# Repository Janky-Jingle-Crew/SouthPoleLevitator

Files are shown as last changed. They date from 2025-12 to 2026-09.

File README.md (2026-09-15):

# South Pole Levitator

Janky Jingle Crew is back this Christmas as well! We are continuing with the theme of magnetic propulsion from last year, but this time for levitation! 

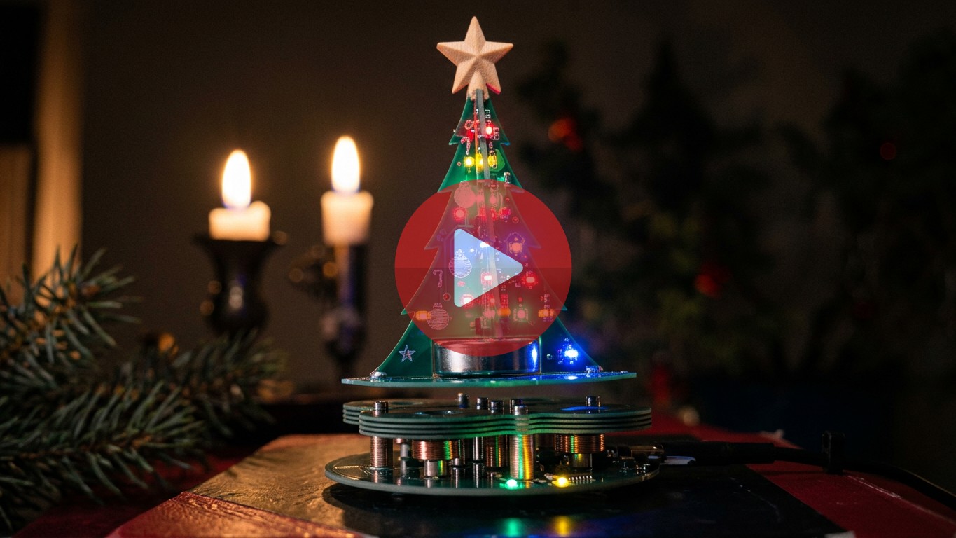
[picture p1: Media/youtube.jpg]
[](https://youtu.be/B3FScckztUA)

## Background
Magnetic levitation kits have been around for a long time, but most of them are analog designs running on 12 V. A more recent 5 V digital version by [Jonathan Lock](https://gitlab.com/e4870/maglev/-/tree/main) caught our attention and served as a big source of inspiration for this project. Our take focuses on lowering the BOM cost and making assembly easier by replacing traditional coils with PCB coils.

We were aiming to build a batch of around 50 units, so coil winding quickly became a bottleneck. That led us to PCB coils as a more scalable solution. Mounting the coils was another pain point, gluing them down and then soldering wires (like many existing kits do) felt messy. Instead, we combined the mounting and electrical connection using solderable standoffs.

We also made a (slightly unnecessary) optimization on the microcontroller side. To reduce BOM cost slightly, we chose the STM32G030, which doesn’t have an FPU, and planned to implement all control algorithms using fixed-point math. In hindsight, the time spent probably outweighed the cost savings, but at least we learned a lot about fixed-point math (and wrote terrible code) along the way.

The final result is shown below: a fully functional magnetic levitation platform made entirely from PCBs. Even the levitating tree is a PCB. Overall, the project turned out well, although there are plenty of things that could still be improved. Feel free to open an issue or mail us if you have any technical questions.

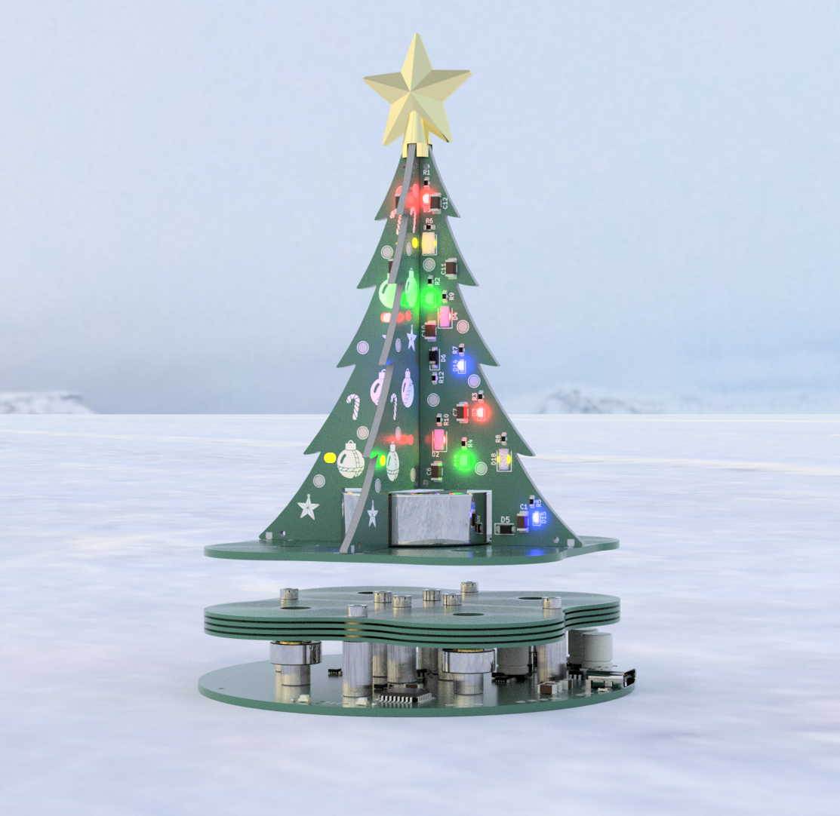
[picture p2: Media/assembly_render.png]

<!-- <img src="./Media/demo.png" width="600px"/> -->
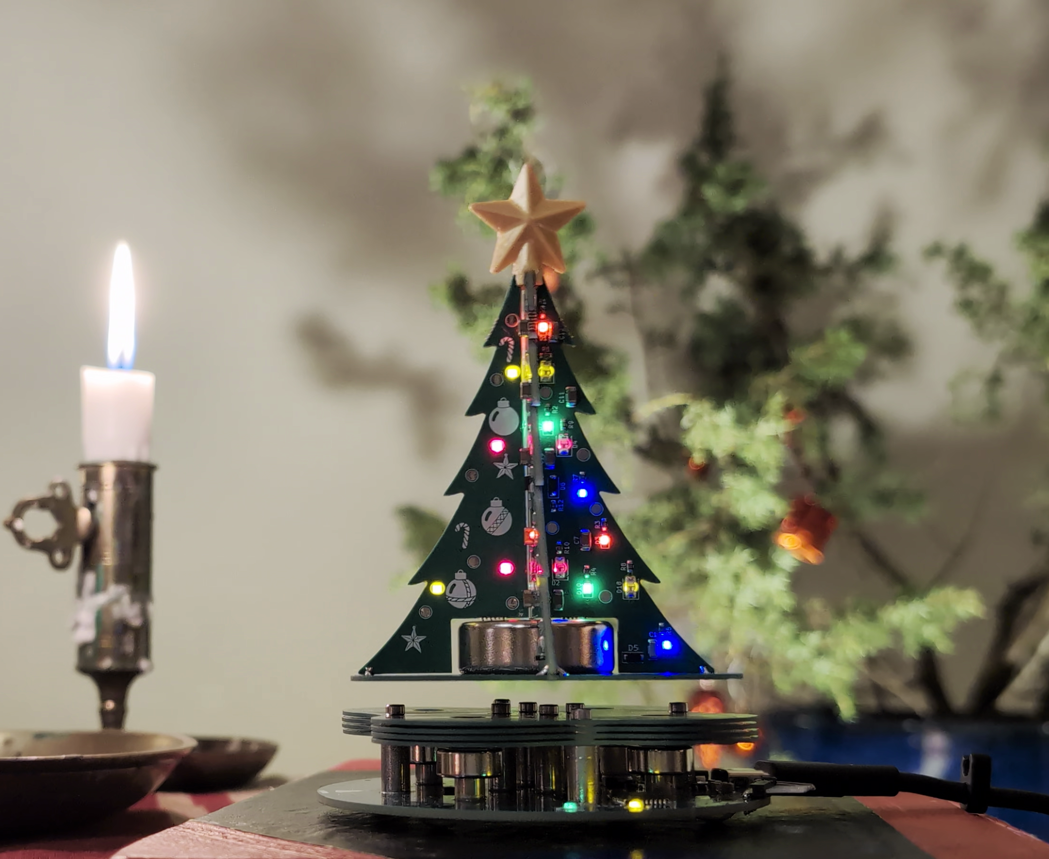
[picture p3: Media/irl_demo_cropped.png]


## User Guide

The card needs to be powered with a 5V power supply over USB-C, capable of at least 500 mA.

To levitate the tree:

1. Place the tree away from the driver board.
2. Place the driver board on a flat, nonmagnetic surface, and plug in the USB-C cable. Note that the board needs to be level when it gets power for the correct calibration. If the tree is too close, this will also affect the calibration. The calibration is complete once you hear a short beep from the coils. The status LED should also start blinking.
3. Hold the tree a few centimeters over and lower it slowly, trying to keep it centered and pointed straight up.
4. The rest is a balance between keeping the tree centered, and holding it with a loose enough grip. The tree needs to have the freedom to find the center itself, while also being prevented from sticking to either of the four base magnets.

It is also possible to play some Christmas tunes. Simply turn the driver board upside down and place the tree on top of it. The coils should start playing a random assortment of Christmas tunes.

## Working principle

### Magnetic levitation
The levitation is generated by four PCB coils but also four neodymium magnets. The base magnets provide the majority of the force required for levitation while the coils only generate a small corrective force required to keep the magnet in a stable position (Earnshaw's theorem). 

Each coil can be driven independently, but we chose to split the coils into two pairs (X & Y) and drive them with opposite polarity.

A 3D Hall effect sensor TMAG5273 was used to sense the position of the levitating magnet and drive the coils accordingly.

### Control

At the core the control algorithm is a PD controller controlling the duty cycle of the coil drivers in order to keep the levitating magnet centered in the X and Y direction. The position is not directly measured, instead the magnetic field strength in the X and Y direction is used as a proxy for position. This is not linear with the actual position, but is approximated as linear close to the center. This is the general idea but there are multiple problems that need to be handled for stable levitation:
<!-- - Non-linear relation between coil driver duty cycle and generated magnetic field. -->
<!-- - Non-linear coil driver characteristics. -->
<!-- - Coupling between coil current and measured magnetic field. -->
<!-- - Setpoint calibration. -->

<details>
<!-- #### Non-linear coil driver characteristics. -->
<summary> Non-linear coil driver characteristics </summary>

We observed a non linear relation between the coil driver duty cycle and the output current which can be seen in the figure below. To correct for this we wanted to measure the coil current as a function of duty cycle. Since coil current is proportional to the generated magnetic field we can measure the strength of the magnetic field for different duty cycles with the hall sensor. From this a quadratic fit was made which is used to linearize the coil driver response in the control algorithm.

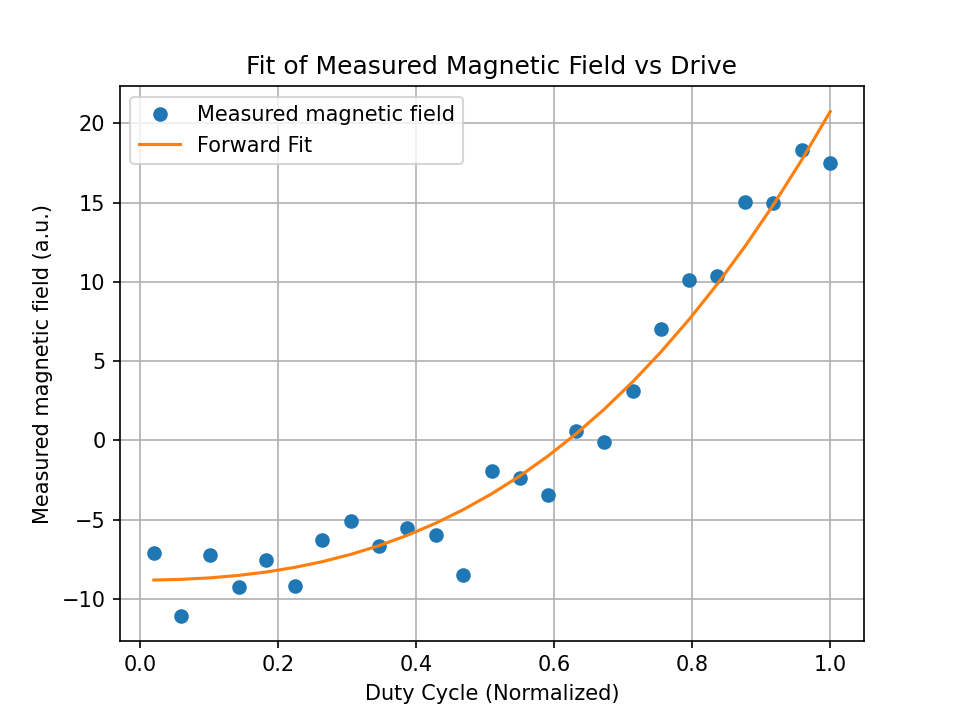
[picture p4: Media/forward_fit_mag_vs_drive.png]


</details>

<details>
<!-- #### Coil coupling compensation -->
<summary> Coupling between coil current and measured magnetic field </summary>

When driving the coils, the generated magnetic field affects the hall sensor measurements. This is problematic since this is added to the field from the levitating magnet and affects the position measurement. Since the position measurement is used as the input to the controller this creates a feedback loop which can lead to instability and oscillations. To compensate for this an feedforward model of the generated magnetic field from the coil current is subtracted from the hall sensor measurements before they are used in the controller. This model is created by measuring the magnetic field from each coil at different duty cycles while there is no levitating magnet present. A linear fit is then made to get the coupling coefficients for each coil. This is done during the initialization of the system.

</details>

<details>
<!-- #### Setpoint calibration -->
<summary> Setpoint calibration </summary>

Due to manufacturing tolerances in the placement of the hall sensor and the base magnets, the center of the base magnetic field, which is the optimal place to levitate the magnet, does not necessarily correspond to above the hall sensor. This means that the setpoint for the controller has to be calibrated for each unit.

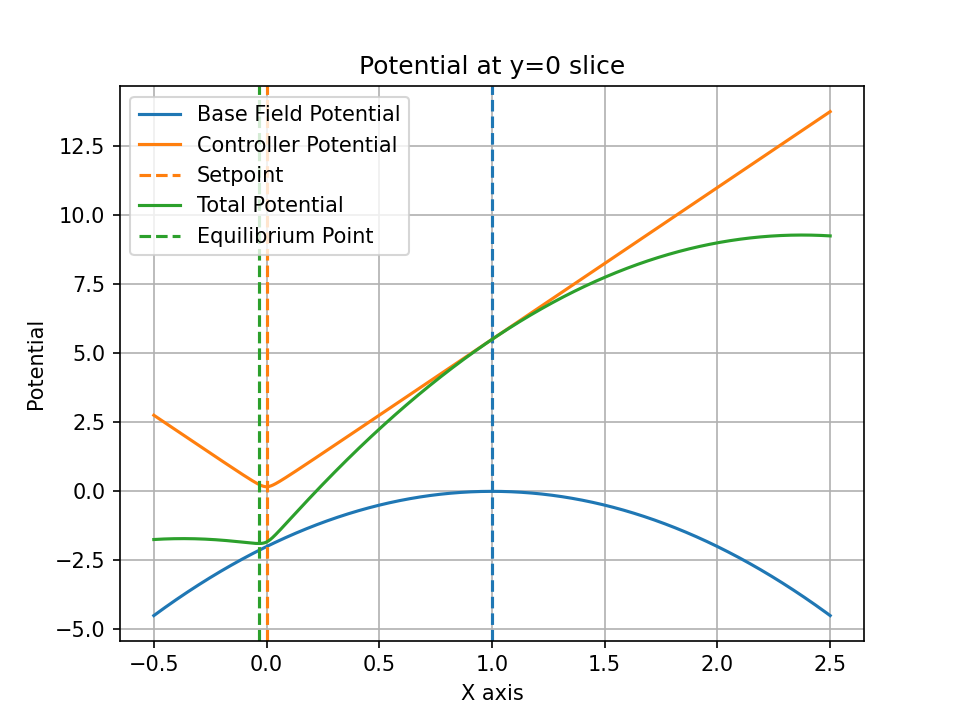
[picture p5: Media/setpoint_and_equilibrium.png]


In the figure above, an illustrative example of the magnetic potential from the base magnets and the proportional part of the PD controller is shown. The blue curve represents the potential from the base magnets, which has a unstable equilibrium point at $x_{base}=1$. The orange curve represents the potential from the proportional part of the controller, which is centered around the setpoint at $x_{setpoint} = 0$. The total potential is the sum of these two potentials, shown in green, which has a stable equilibrium point close to but not exactly at the setpoint. Due to the slope of the base potential at the setpoint, the equilibrium point will be offset the setpoint away from the base magnet center. By calculating this difference $x_{delta} = x_{equilibrium} - x_{setpoint}$ we can then adjust the setpoint $x_{setpoint,new} = x_{setpoint} + \alpha x_{delta}$ to move the equilibrium point closer to the setpoint. This process is repeated every control loop and will lead to the setpoint converging to the base magnet center.

</details>

### Driving LEDs wirelessly

The LEDs on the tree are powered by electro-magnetic noise from the switching ripple of the coils on the driver board. There are four PCB coils in the base of the tree, each powering its quarter. The induced AC voltage in each of these coils is amplified with a resonant LC-tank tuned to the switching frequency. The resonance circuit consists of the inductance in the PCB coil and a separate MLCC C0G capacitor on the tree quarter. This amplified waveform is then rectified with a single Schottky diode, finally driving the LEDs. The power transfer efficiency is absolutely garbage and therefore the LEDs will only light up when the coils are aligned. However, this also gives a passive blinking/strobing effect when it spins (without any additional components)! Definitely a planned feature and not a design flaw....

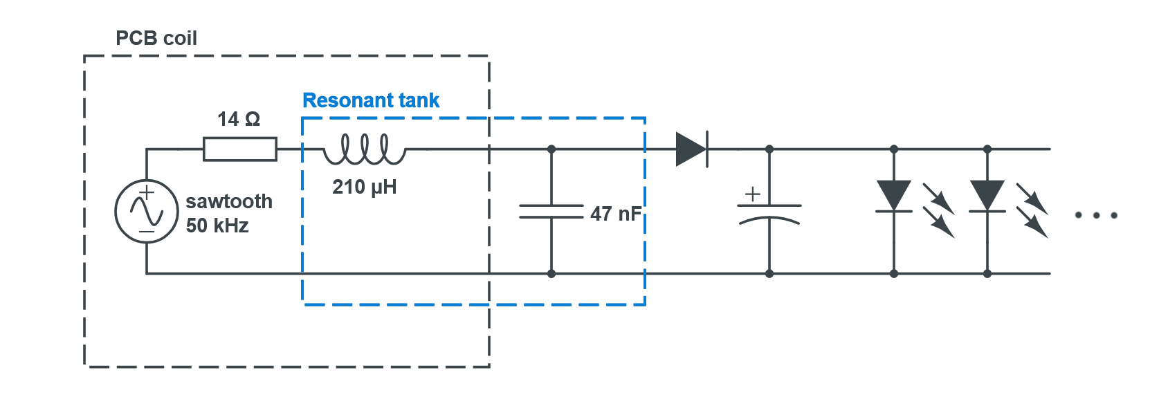
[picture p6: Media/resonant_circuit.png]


## Design
The whole levitator can be split into two main parts. The platform base and the levitating tree. The platform base consists of two different PCB designs, one driver PCB and four coil PCBs (4x).

### Driver board
The driver board has all the components mounted. There are a total of 12 standoffs: 8x M2 standoffs for mounting the coil board and 4x M3 standoffs for mounting the base magnets. An STM32G030 reads the XYZ magnetic fields from the TMAG5273 and controls 4x DRV8837 drivers for the coils. Power is provided by USB-C connector. A TagConnect TC2030 along with pin headers break out the SWD pins for debugging.

### Coil board
The coil board consists of four spiral coils with ~116 turns and 0.245mm trace width (25 turns per layer, 4-layer PCB, outer 1 oz, inner 1 oz). The resulting coil resistance turns out to be around 20 Ohm. Therefore, 4x coils are connected in parallel to enable higher coil current and also increase efficiency slightly. Brass washers are placed in-between each coil board to ensure electrical contact all the way down to the driver board. Initially a coil with 100 turns and 0.3mm trace width was used (outer 1 oz, inner 0.5 oz). This worked fine as well and 0.5oz is way cheaper. You can use either one, although the code might be slightly more tuned for the 116 turns variant, it should still work with the cheaper 100 turns variant.

### Tree
The tree consists of 5 PCBs, four of which constitute the tree itself, and one being the base plate with the pickup coils. A 3D-printed star keeps all of the tree-PCBs connected at the top! Tip: blow on one side of the tree when it is levitating to make it spin!

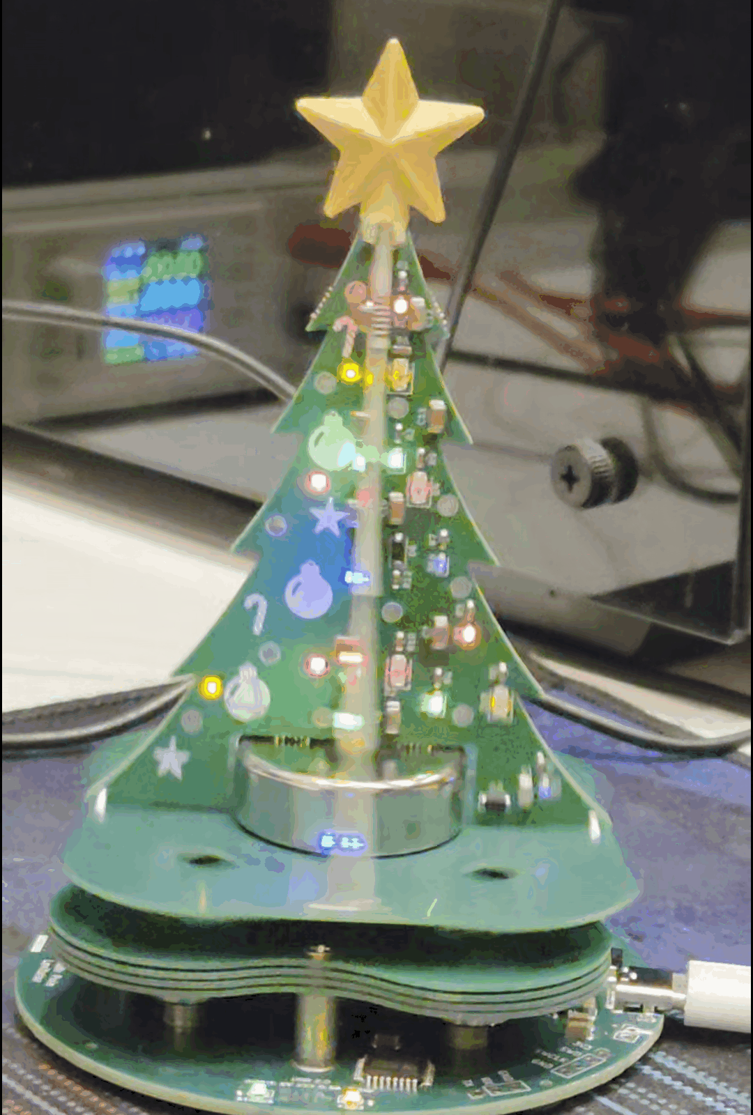
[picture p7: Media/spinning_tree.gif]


## Manufacturing
All the manufacturing files for the PCBs and the final software can be found in this repository. 

Upload these to your favorite PCB manufacturer and order the boards. We designed the boards with JLCPCBs preexisting Parts Lib and used their PCBA due to time constraints. However, PCBWay and NextPCB probably have these components in stock as well or can source them for you.

You will also need the following materials per unit:
- 1x Levitation magnet (N35-N45 30mm diameter, 10mm height) 
- 4x Ring magnets with M3 countersunk hole (N35-N45, 12mm diameter, 5mm height)
- 8x Non-magnetic M2 screws 8mm
- 4x Non-magnetic M3 countersunk screws 8mm
- 24x M2 Brass washers 4-5mm OD (steel probably works as well, slightly worse conductivity).
- 8x Rubber feet (at least 0.4mm height)

## Assembly

### Driver board

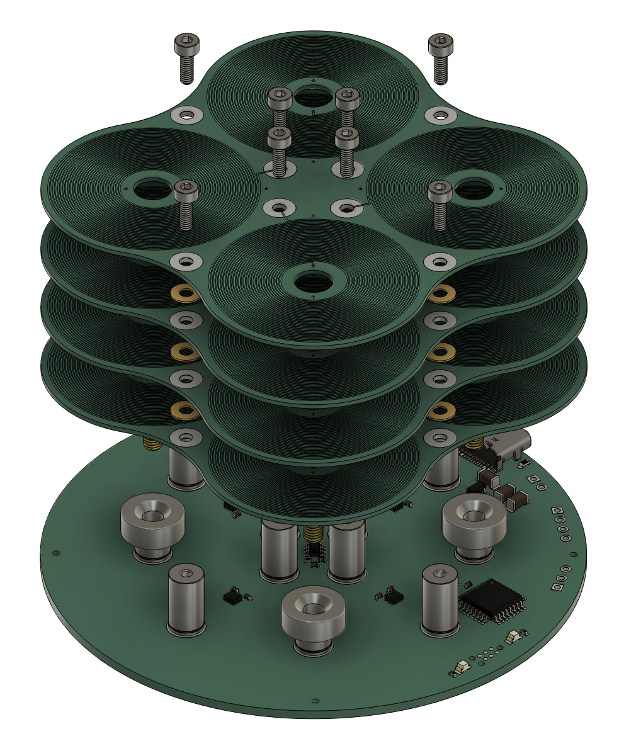
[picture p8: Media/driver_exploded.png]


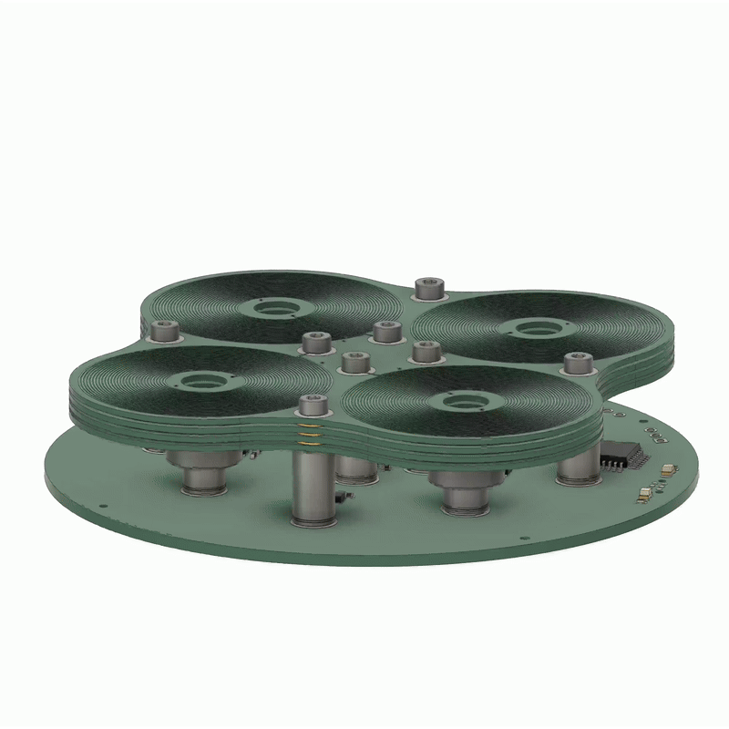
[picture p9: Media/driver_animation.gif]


### Tree

To begin with, the star is 3D-printed. You can either use the half-star variant (recommended) or the whole-star variant. For the half-star, print two of them laying flat and with support activated. The halves can then be glued together with superglue. Alternatively, the whole-star variant can be printed standing up depending on how well your printer handles overhang and/or surface finishes over supports.

<p align="center">
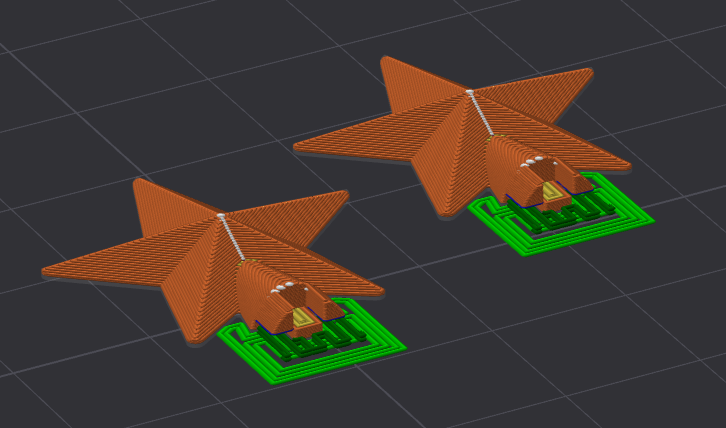
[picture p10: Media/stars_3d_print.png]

</p>

To keep the magnet centered, and the parts of the tree perpendicular to the base, a 3D-printed jig was used. This is not necessary, but drastically reduces the time to assemble multiple trees. If you are only making one, don't bother printing out the jig.

Both the magnet and the star can be glued with e.g. superglue or epoxy. Note that the magnet orientation matters!

The four "quarters" of the tree are soldered onto the base PCB with two solder joints each. These joints are the PCB coil A & B. We recommend gluing the star before soldering!



## FAQ

### How do I reproduce this?
PCB assembly files can be found in /production for the driver board and tree in their respective folders under PCB/. 
Gerber files for both coil boards are found in /gerber in their respective folders under PCB/. Remember to choose 1oz inner layers if you go for 116 turns variant.
Upload to your PCB manufacture of choice (JLCPCB, PCBWay, NextPCB).
Print the star. Buy magnets and screws. Assemble.

#### Flashing
An STLink, Segger Jlink or similar is required to flash the driver board. Some type of 6 pin (2x3 1.27mm pitch) pogo connector is also required (we use a TagConnect TC2030NL).
Or you can use the through hole SWD pins. A compiled binary is provided in SW/release if you don't want to go through the hassle of compiling yourself because the makefile is a bit of mess currently. It's written for a Windows filesystem but uses unix commands (we used msys2 or cmder to compile). Next project will probably use cmake to avoid these problems.

### How much did this all cost?
This year's project was quite expensive. Even with a big batch of 50 units, the unit cost was around 40-50 EUR. PCBs alone cost 20 EUR per unit. Magnets and screws were not cheap either.
Expect to spend quite a bit if you are planning on reproducing it, especially a small batch. 

## Acknowledgements
Special thanks to Jonathan Lock, this project was heavily inspired by his well-documented [maglev build](https://gitlab.com/e4870/maglev/-/tree/main).

Also thanks to Seth.K and his [coil generator plugin for KiCAD](https://github.com/SK-Electronics-Consulting/kicad-coil-generators). 

## Credits
The Janky Jingle Crew 2025 consists of:

 - [Daniel Quach](https://github.com/BasementCircuits): Project lead, PCB, Firmware
 - [Johan Wheeler](https://github.com/johanwheeler): Firmware, Control
 - [Gustav Abrahamsson](https://github.com/GustavAbrahamsson): PCB, Mechanical
 - [Adam Anderson](https://github.com/adaand00): Firmware

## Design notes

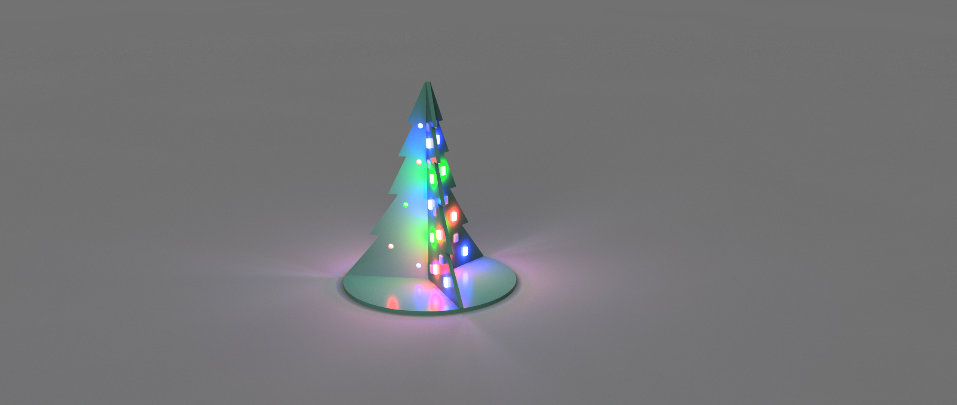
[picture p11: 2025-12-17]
Media/floating_tree_concept.png

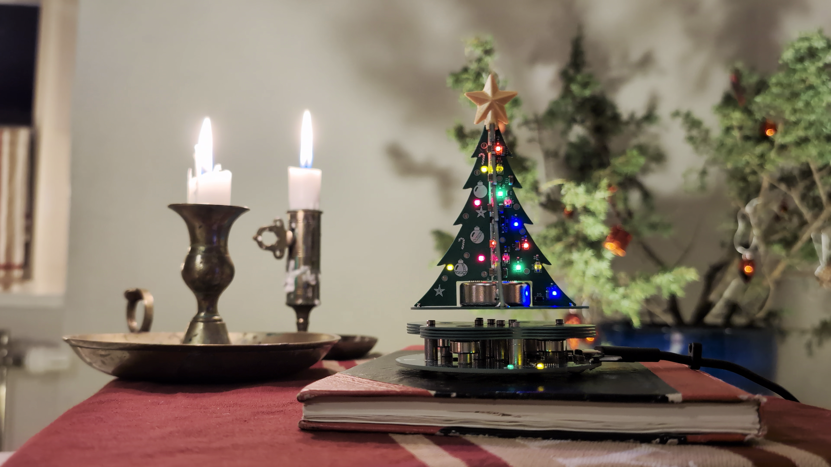
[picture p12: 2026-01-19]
Media/irl_demo.png

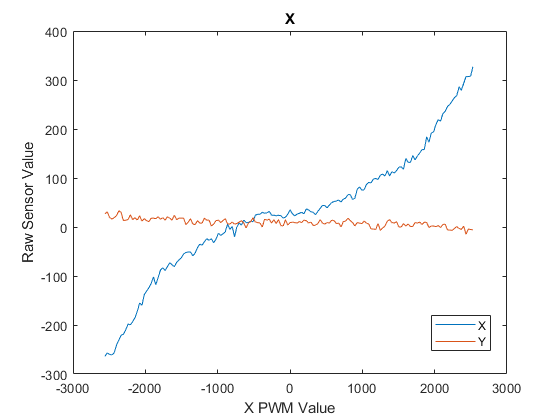
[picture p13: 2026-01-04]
SW/X_map.png

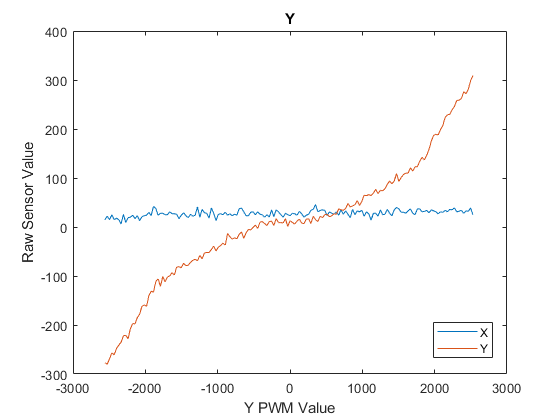
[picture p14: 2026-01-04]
SW/Y_map.png

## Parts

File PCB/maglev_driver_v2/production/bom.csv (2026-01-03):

Designator | Footprint | Quantity | Value | LCSC Part #
C1, C2, C22, C3, C8 | 1206 | 5 | 10u | C13585
C10, C11, C12, C14, C15, C16, C17, C18, C19, C20, C21, C9 | 0402 | 12 | 100n | C307331
C13 | 1206 | 1 | 4.7u | C29823
C4, C5, C6, C7 | C_Elec_6.3x7.7 | 4 | 470u | C46550459
D1 | D_SMB | 1 | P6SMB6.8CA | C78395
D2 | 0805 | 1 | 3V3_ON | C2296
D4 | 0805 | 1 | STATUS | C2297
H1 | SMTSO20 | 1 | XP+ | C2928171
H12, H13, H14, H15 | SMTSO30 | 4 | M3 | C2915635
H2 | SMTSO20 | 1 | XN+ | C2928171
H3 | SMTSO20 | 1 | XP- | C2928171
H4 | SMTSO20 | 1 | XN- | C2928171
H5 | SMTSO20 | 1 | YP+ | C2928171
H6 | SMTSO20 | 1 | YN+ | C2928171
H7 | SMTSO20 | 1 | YP- | C2928171
H8 | SMTSO20 | 1 | YN- | C2928171
J1 | USB_C_Receptacle_HRO_TYPE-C-31-M-12 | 1 | TYPE-C-31-M-12 | C165948
R1, R7 | 0402 | 2 | 3.3k | C25890
R2, R3 | 0603 | 2 | 5.1k | C23186
R4, R5, R6 | 0402 | 3 | 2.2k | C25879
U1 | SOT-23-3 | 1 | XC6206P332MR-G | C5446
U2 | SOT-23-5 | 1 | TPS2069CDBV | C181752
U3, U4, U7, U8 | WSON-8-1EP_2x2mm_P0.5mm_EP0.9x1.6mm | 4 | DRV8837 | C39159
U6 | SOT-23-6 | 1 | TMAG5273 | C3716049
U9 | LQFP-32_7x7mm_P0.8mm | 1 | STM32G030K6T6 | C529331

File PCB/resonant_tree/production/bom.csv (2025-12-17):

Designator | Footprint | Quantity | Value | LCSC Part #
C1 | 1206 | 1 | 47n | C21812
C10, C11, C12, C6, C7 | 1206 | 5 | 10u | C13585
D1, D3 | 0603 | 2 | Red | C2286
D10, D7 | 0805 | 2 | Green | C2297
D14, D15 | 0603 | 2 | Blue | C2288
D17, D18 | 1206 | 2 | Yellow (rev) | C125108
D2, D4 | 1206 | 2 | Red (rev) | C125107
D5 | D_SOD-123F | 1 | RB161MM-20TR | C123070
D6 | D_SOD-123 | 1 | BZT52C3V3 | C19077396
R1, R3 | 0603 | 2 | 1.5K | C22843
R10, R6, R8, R9 | 0603 | 4 | 1K | C21190
R12 | 0603 | 1 | 390 | C23151
R2, R4 | 0603 | 2 | 4K7 | C23162
R5, R7 | 0603 | 2 | 300 | C23025

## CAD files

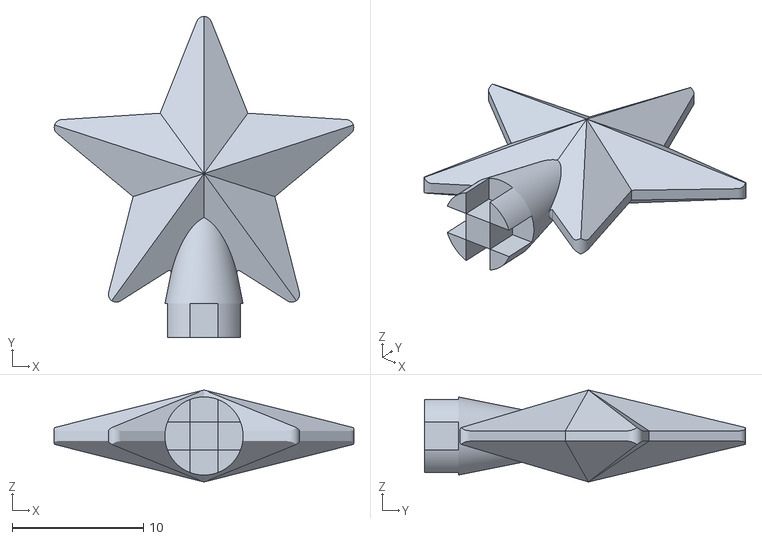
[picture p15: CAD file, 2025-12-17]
CAD/star_whole.stl
22.8 x 24.5 x 7.00

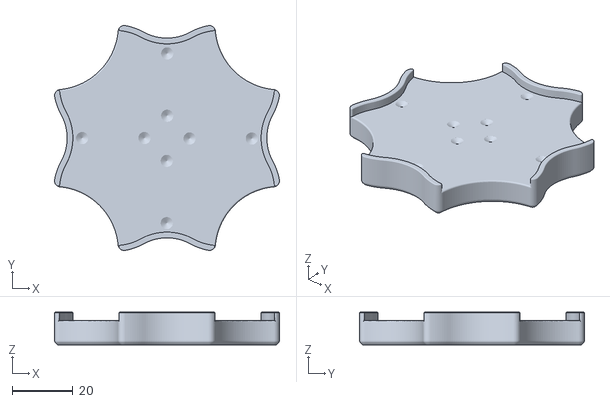
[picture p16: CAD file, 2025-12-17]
CAD/assembly_and_jigs/coil_jig.stl
74.1 x 74.1 x 10.8

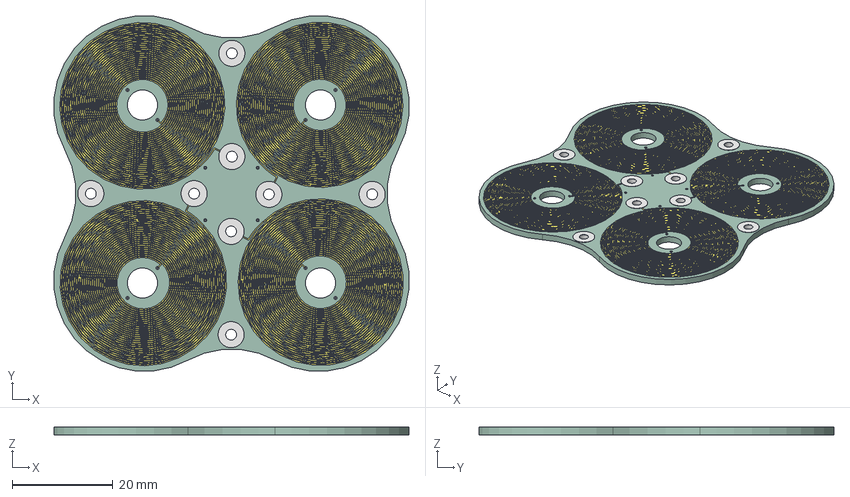
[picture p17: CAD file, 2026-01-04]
PCB/maglev_coils_v2/maglev_coils_v2.step
70.5 x 70.5 x 1.59 mm
maglev_coils_copper
maglev_coils_pad
maglev_coils_PCB

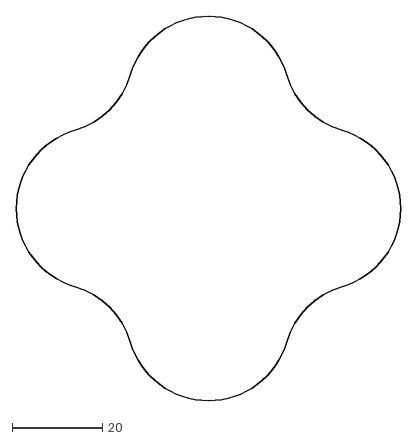
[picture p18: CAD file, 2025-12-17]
PCB/maglev_coils_v2/pcb_coils/outline.dxf
85.0 x 85.0

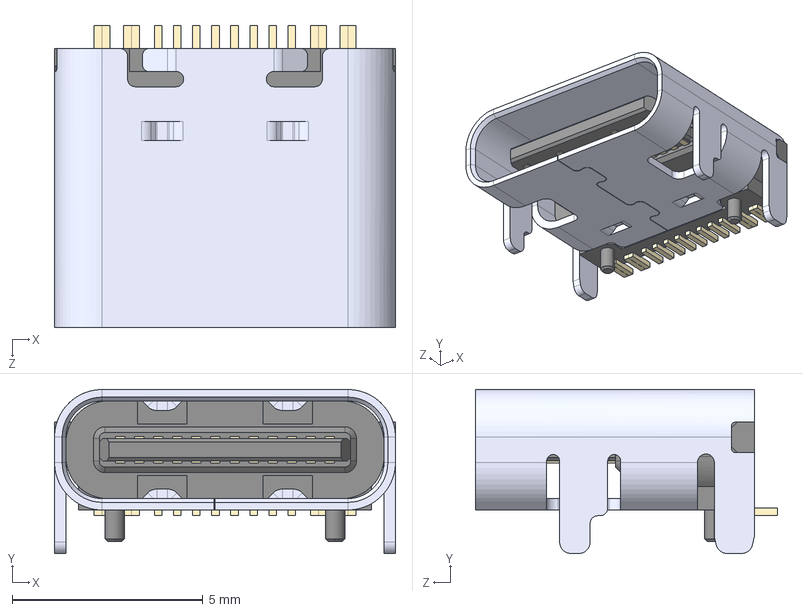
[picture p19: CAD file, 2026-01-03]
PCB/maglev_driver_v2/custom_fp/TYPE-C-31-M-12.step
8.94 x 4.30 x 7.90 mm

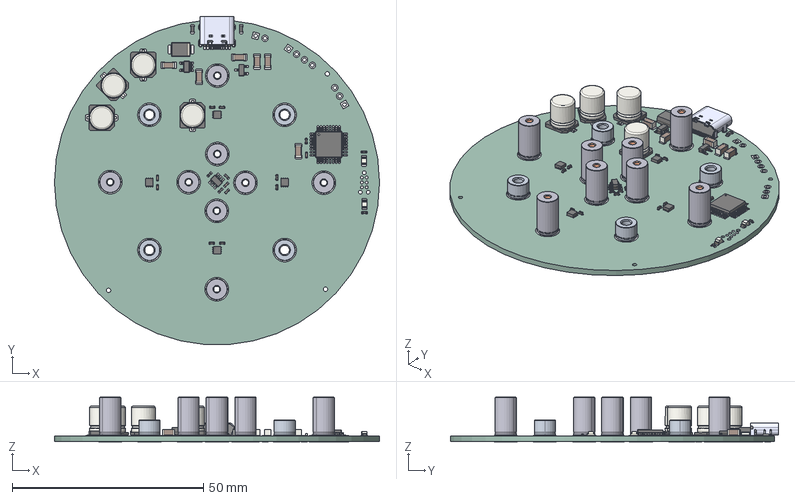
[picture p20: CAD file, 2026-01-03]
PCB/maglev_driver_v2/maglev_driver_v2.step
85.0 x 85.8 x 11.7 mm
WSON-8-1EP_2x2mm_P0.5mm_EP0.9x1.6mm x 4
SMTSO-M2-10ET-PennEngineering-3D-08-23-2025 x 8
SMTSO-M3-4ET-PennEngineering-3D-11-19-2025 x 4
C_0402_1005Metric x 12
D_SMB
C_1206_3216Metric x 6
LQFP-32_7x7mm_P0.8mm
LED_0805_2012Metric x 2
R_0603_1608Metric x 2
R_0402_1005Metric x 5
SOT-23-5
C_Elec_6.3x7.7 x 4
SOT-23-6
SOT-23-3
TYPE-C-31-M-12
maglev_driver_pad
maglev_driver_PCB

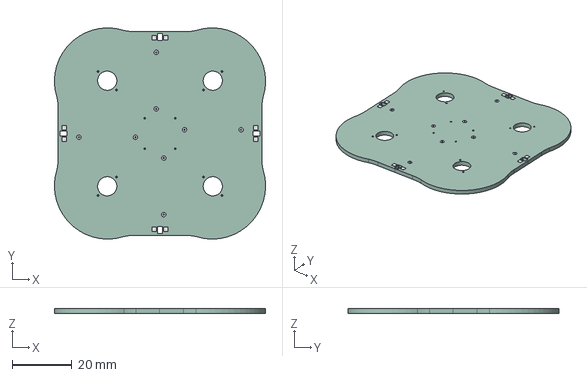
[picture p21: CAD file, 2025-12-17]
PCB/quad_coils/quad_coils.step
70.4 x 70.4 x 1.59 mm
quad_coils_pad
quad_coils_PCB

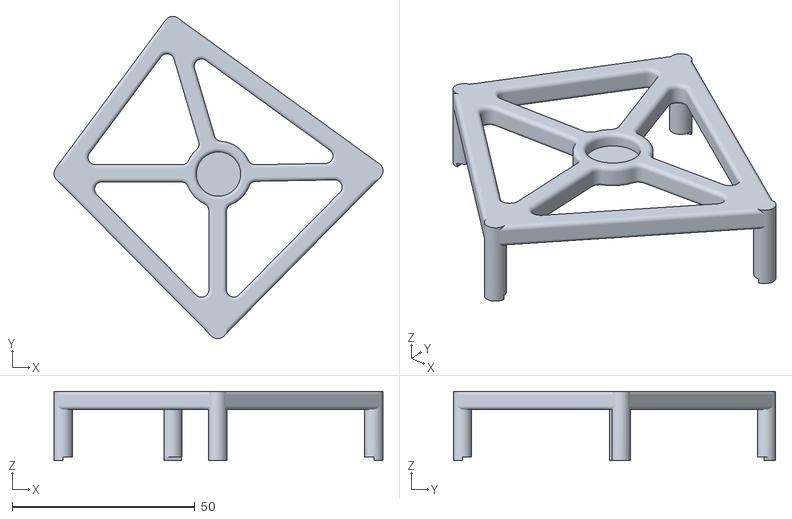
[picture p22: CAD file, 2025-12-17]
CAD/assembly_and_jigs/magnet_frame.stl
90.0 x 88.1 x 19.0

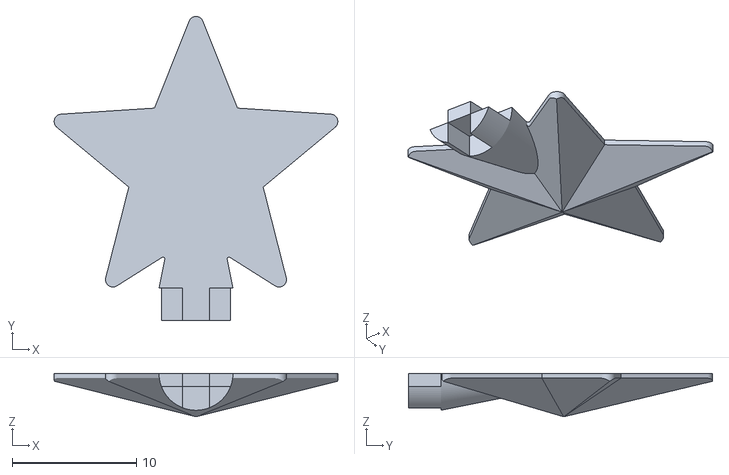
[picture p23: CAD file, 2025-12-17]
CAD/star_half.stl
22.8 x 24.5 x 3.50

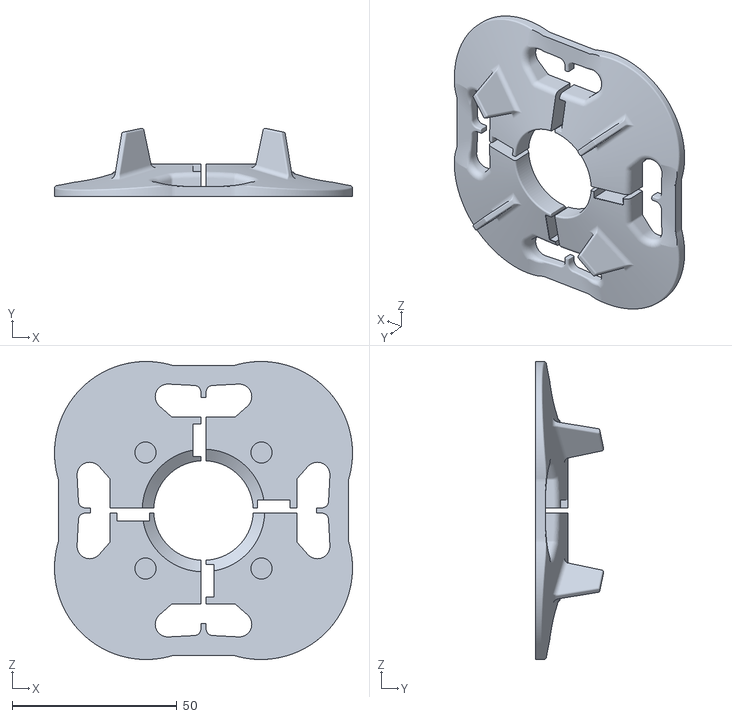
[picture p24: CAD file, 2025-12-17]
CAD/assembly_and_jigs/tree_frame.stl
90.4 x 20.5 x 90.4

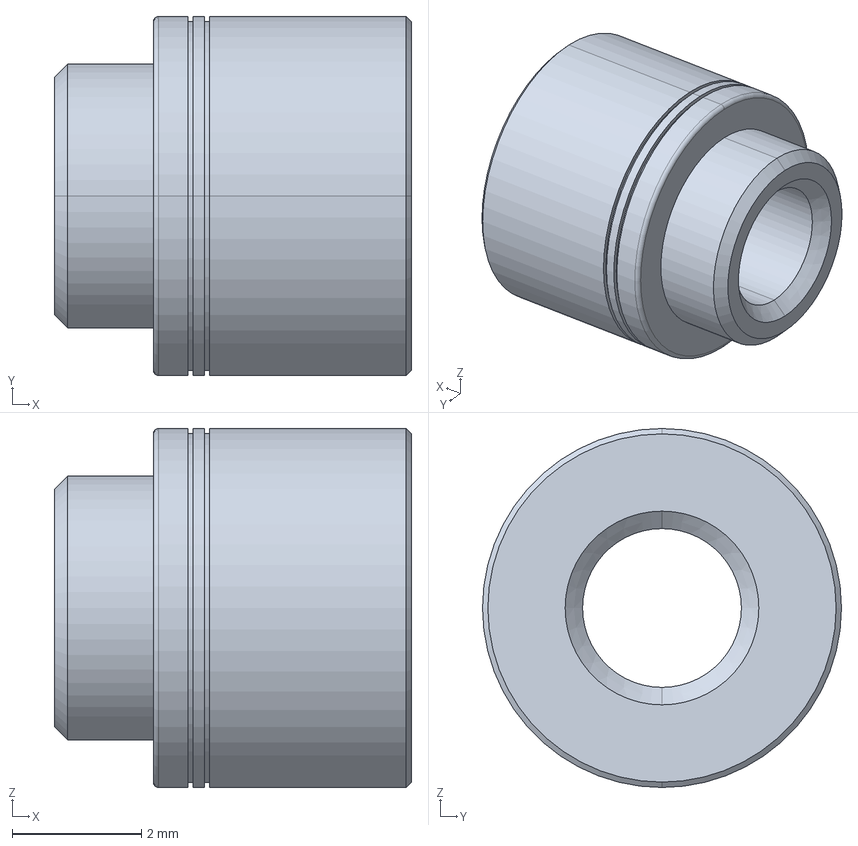
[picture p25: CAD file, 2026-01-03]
PCB/maglev_driver_v2/custom_fp/SMTSO-M3-4ET-PennEngineering-3D-11-19-2025.stp
5.53 x 5.56 x 5.56 mm

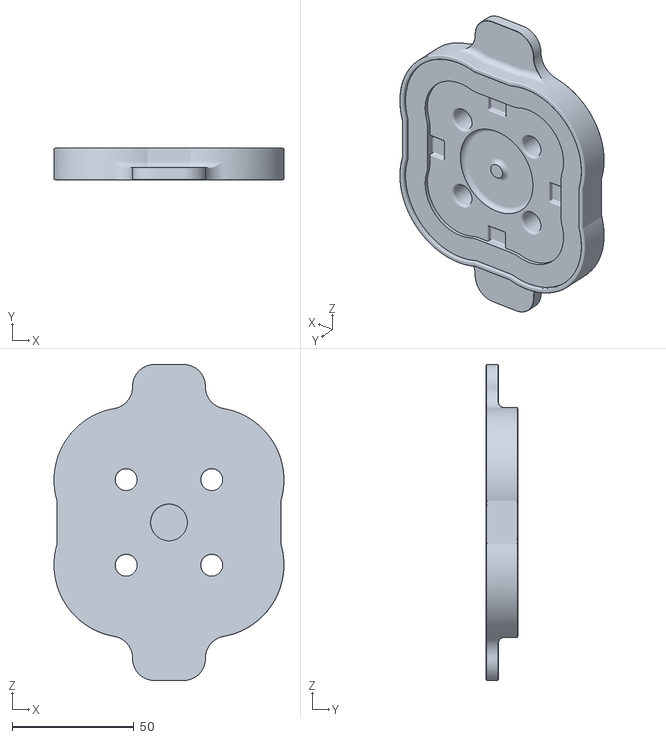
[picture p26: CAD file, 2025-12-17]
CAD/assembly_and_jigs/tree_base.stl
94.6 x 13.0 x 130.0

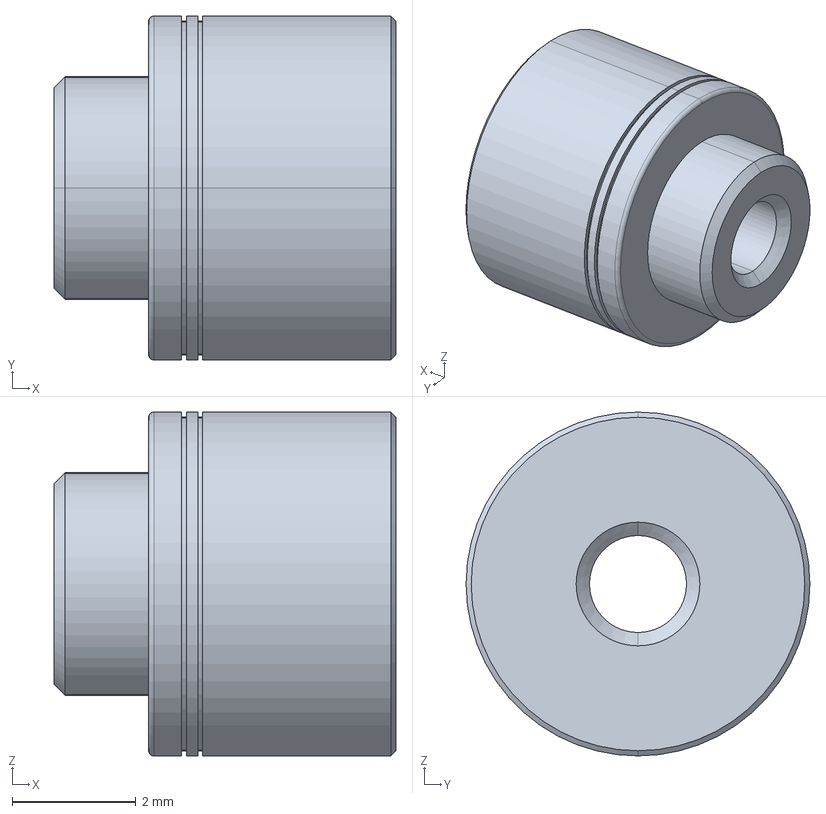
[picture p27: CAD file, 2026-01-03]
PCB/maglev_driver_v2/custom_fp/SMTSO-M2-4ET-PennEngineering-3D-11-19-2025.stp
5.53 x 5.56 x 5.56 mm

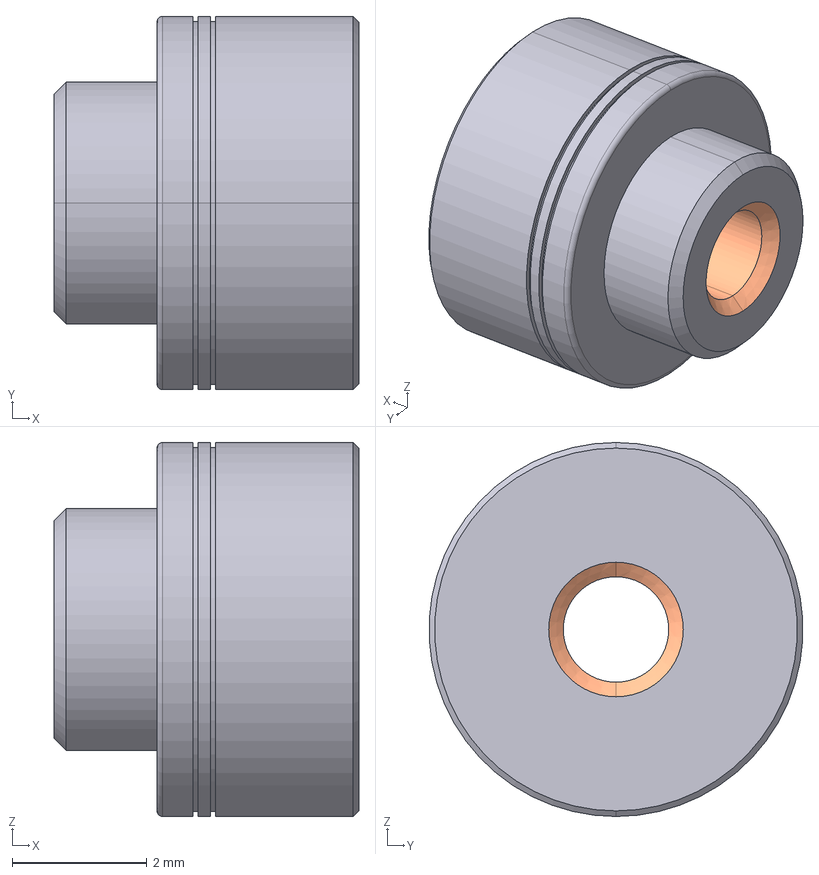
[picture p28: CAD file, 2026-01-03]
PCB/maglev_driver_v2/custom_fp/SMTSO-M2-3ET-PennEngineering-3D-05-11-2025.stp
4.53 x 5.55 x 5.56 mm

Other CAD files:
PCB/maglev_driver_v2/custom_fp/SMTSO-M2-10ET-PennEngineering-3D-08-23-2025.stp
PCB/maglev_driver_v2/custom_fp/JS102011SAQN--3DModel-Eagle-1.STEP

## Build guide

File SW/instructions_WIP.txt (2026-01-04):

Install the following and add to PATH (windows):
Linux users already know what to do.

GNU Arm Embedded Toolchain (arm-none-eabi-gcc.exe, arm-none-eabi-objcopy.exe) 
Add the bin folder containing these executables to PATH.
Use GCC11 or higher

Gnu Make for windows, use GnuWin32
Add the bin folder containing make.exe to PATH.

ST-LINK Utility
Add folder containing ST-LINK_CLI.exe to PATH.

Run "make flash" in conemu/cmder or similar terminal to build and upload code.
Otherwise you can flash with your tool of choice (ST-LINK Utility/PyOCD/OpenOCD) with the precompiled binary in /release
RTT printouts can be read with "make rtt" (requires python and pyOCD)

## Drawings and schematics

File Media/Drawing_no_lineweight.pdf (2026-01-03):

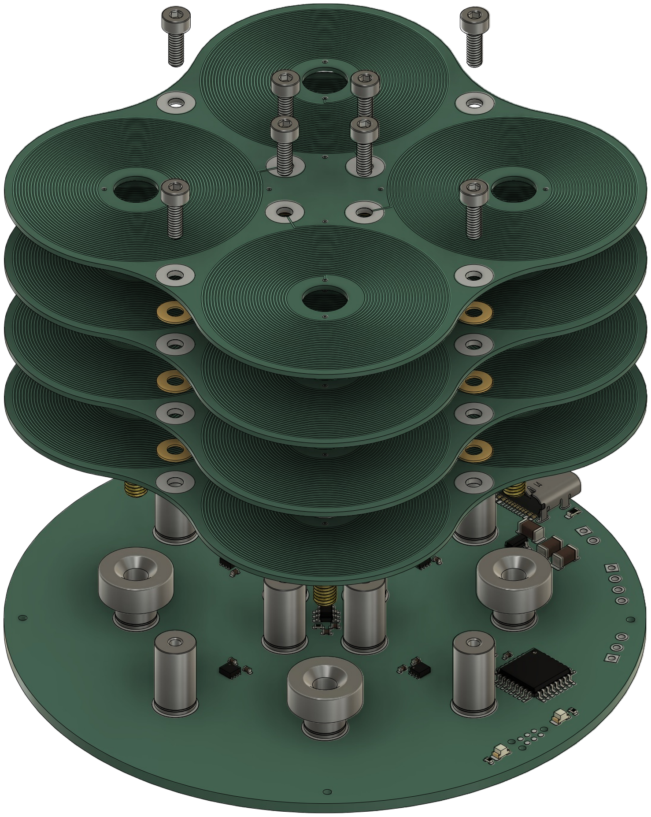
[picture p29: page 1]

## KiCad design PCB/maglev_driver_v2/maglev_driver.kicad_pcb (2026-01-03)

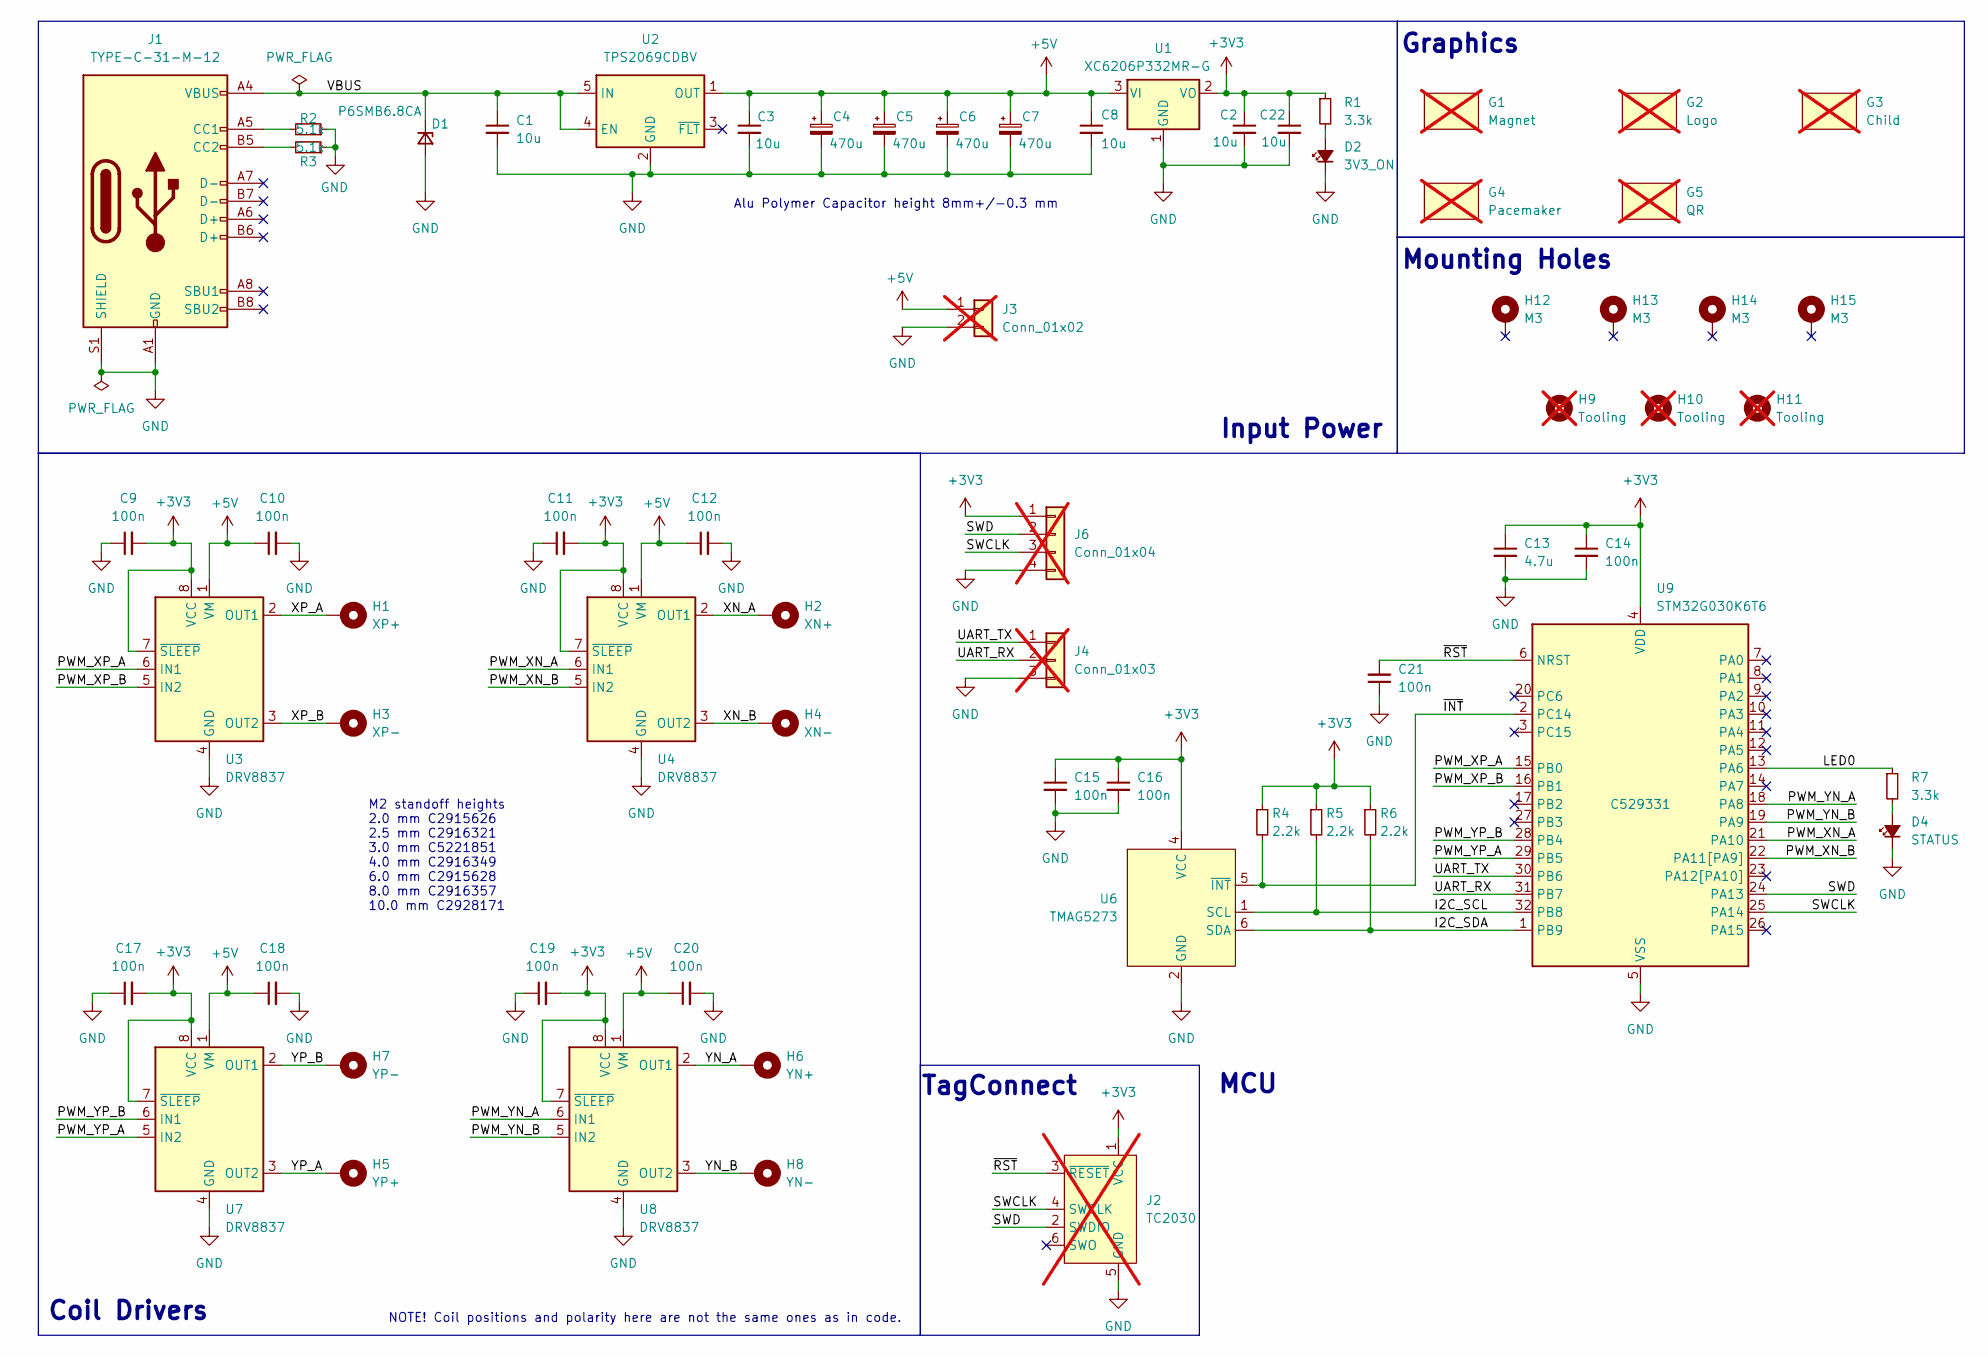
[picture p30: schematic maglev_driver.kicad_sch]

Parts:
C1, C2, C3, C8, C22: 10u; C_1206_3216Metric; MPN C13585
C4, C5, C6, C7: 470u; C_Elec_6.3x7.7; MPN C46550459
C9, C10, C11, C12, C14, C15, C16, C17, C18, C19, C20, C21: 100n; C_0402_1005Metric; MPN C307331
C13: 4.7u; C_1206_3216Metric; MPN C29823
D1: P6SMB6.8CA; D_SMB; MPN C78395
D2: 3V3_ON; LED_0805_2012Metric; MPN C2296
D4: STATUS; LED_0805_2012Metric; MPN C2297
G1: Magnet; mag_warning_7_7_mm; not fitted
G2: Logo; tree_7_9; not fitted
G3: Child; child_warning_7_8_mm; not fitted
G4: Pacemaker; pacemaker_warning_7_7_mm; not fitted
G5: QR; qr_25mm; not fitted
H1: XP+; SMTSO20; MPN C2928171
H2: XN+; SMTSO20; MPN C2928171
H3: XP-; SMTSO20; MPN C2928171
H4: XN-; SMTSO20; MPN C2928171
H5: YP+; SMTSO20; MPN C2928171
H6: YN+; SMTSO20; MPN C2928171
H7: YP-; SMTSO20; MPN C2928171
H8: YN-; SMTSO20; MPN C2928171
H9, H10, H11: Tooling; tooling_hole; not fitted
H12, H13, H14, H15: M3; SMTSO30; MPN C2915635
J1: TYPE-C-31-M-12; USB_C_Receptacle_HRO_TYPE-C-31-M-12; MPN C165948
J2: TC2030; Tag-Connect_TC2030-IDC-NL_2x03_P1.27mm_Vertical; not fitted
J3: Conn_01x02; PinHeader_1x02_P2.54mm_Vertical; not fitted
J4: Conn_01x03; PinHeader_1x03_P2.54mm_Vertical; not fitted
J6: Conn_01x04; PinHeader_1x04_P2.54mm_Vertical; not fitted
R1, R7: 3.3k; R_0402_1005Metric; MPN C25890
R2, R3: 5.1k; R_0603_1608Metric; MPN C23186
R4, R5, R6: 2.2k; R_0402_1005Metric; MPN C25879
U1: XC6206P332MR-G; SOT-23-3; MPN C5446
U2: TPS2069CDBV; SOT-23-5; MPN C181752
U3, U4, U7, U8: DRV8837; WSON-8-1EP_2x2mm_P0.5mm_EP0.9x1.6mm; MPN C39159
U6: TMAG5273; SOT-23-6; MPN C3716049
U9: STM32G030K6T6; LQFP-32_7x7mm_P0.8mm; MPN C529331

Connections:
+3V3: C2.1, C9.2, C11.2, C13.1, C14.1, C15.1, C16.1, C17.2, C19.2, C22.1, J2.1 (VCC), J6.1, R1.1, R4.1, R5.1, R6.1, U1.2 (VO), U3.7 (~SLEEP), U3.8 (VCC), U4.7 (~SLEEP), U4.8 (VCC), U6.4 (VCC), U7.7 (~SLEEP), U7.8 (VCC), U8.7 (~SLEEP), U8.8 (VCC), U9.4 (VDD)
+5V: C3.1, C4.1, C5.1, C6.1, C7.1, C8.1, C10.1, C12.1, C18.1, C20.1, J3.1, U1.3 (VI), U2.1 (OUT), U3.1 (VM), U4.1 (VM), U7.1 (VM), U8.1 (VM)
/I2C_SCL: R5.2, U6.1 (SCL), U9.32 (PB8)
/I2C_SDA: R6.2, U6.6 (SDA), U9.1 (PB9)
/LED0: R7.1, U9.13 (PA6)
/PWM_XN_A: U4.6 (IN1), U9.21 (PA10)
/PWM_XN_B: U4.5 (IN2), U9.22 (PA11[PA9])
/PWM_XP_A: U3.6 (IN1), U9.15 (PB0)
/PWM_XP_B: U3.5 (IN2), U9.16 (PB1)
/PWM_YN_A: U8.6 (IN1), U9.18 (PA8)
/PWM_YN_B: U8.5 (IN2), U9.19 (PA9)
/PWM_YP_A: U7.5 (IN2), U9.29 (PB5)
/PWM_YP_B: U7.6 (IN1), U9.28 (PB4)
/SWCLK: J2.4 (SWCLK), J6.3, U9.25 (PA14)
/SWD: J2.2 (SWDIO), J6.2, U9.24 (PA13)
/UART_RX: J4.2, U9.31 (PB7)
/UART_TX: J4.1, U9.30 (PB6)
/VBUS: C1.1, D1.1 (K), J1.A4 (VBUS), J1.A9 (VBUS), J1.B4 (VBUS), J1.B9 (VBUS), U2.4 (EN), U2.5 (IN)
/XN_A: H2.1, U4.2 (OUT1)
/XN_B: H4.1, U4.3 (OUT2)
/XP_A: H1.1, U3.2 (OUT1)
/XP_B: H3.1, U3.3 (OUT2)
/YN_A: H6.1, U8.2 (OUT1)
/YN_B: H8.1, U8.3 (OUT2)
/YP_A: H5.1, U7.3 (OUT2)
/YP_B: H7.1, U7.2 (OUT1)
/~INT: R4.2, U6.5 (~INT), U9.2 (PC14)
/~RST: C21.2, J2.3 (~RESET), U9.6 (NRST)
GND: C1.2, C2.2, C3.2, C4.2, C5.2, C6.2, C7.2, C8.2, C9.1, C10.2, C11.1, C12.2, C13.2, C14.2, C15.2, C16.2, C17.1, C18.2, C19.1, C20.2, C21.1, C22.2, D1.2 (A), D2.1 (K), D4.1 (K), J1.A1 (GND), J1.A12 (GND), J1.B1 (GND), J1.B12 (GND), J1.S1 (SHIELD), J2.5 (GND), J3.2, J4.3, J6.4, R2.1, R3.1, U1.1 (GND), U2.2 (GND), U3.4 (GND), U3.9 (GND), U4.4 (GND), U4.9 (GND), U6.2 (GND), U6.3 (GND), U7.4 (GND), U7.9 (GND), U8.4 (GND), U8.9 (GND), U9.5 (VSS)
unnamed: D2.2 (A), R1.2
unnamed: D4.2 (A), R7.2
unnamed: J1.A5 (CC1), R2.2
unnamed: J1.B5 (CC2), R3.2

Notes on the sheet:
NOTE! Coil positions and polarity here are not the same ones as in code.
MCU
Graphics
Coil Drivers
Alu Polymer Capacitor height 8mm+/-0.3 mm
M2 standoff heights 2.0 mm C2915626 2.5 mm C2916321 3.0 mm C5221851 4.0 mm C2916349 6.0 mm C2915628 8.0 mm C2916357 10.0 mm C2928171
Mounting Holes
TagConnect
Input Power

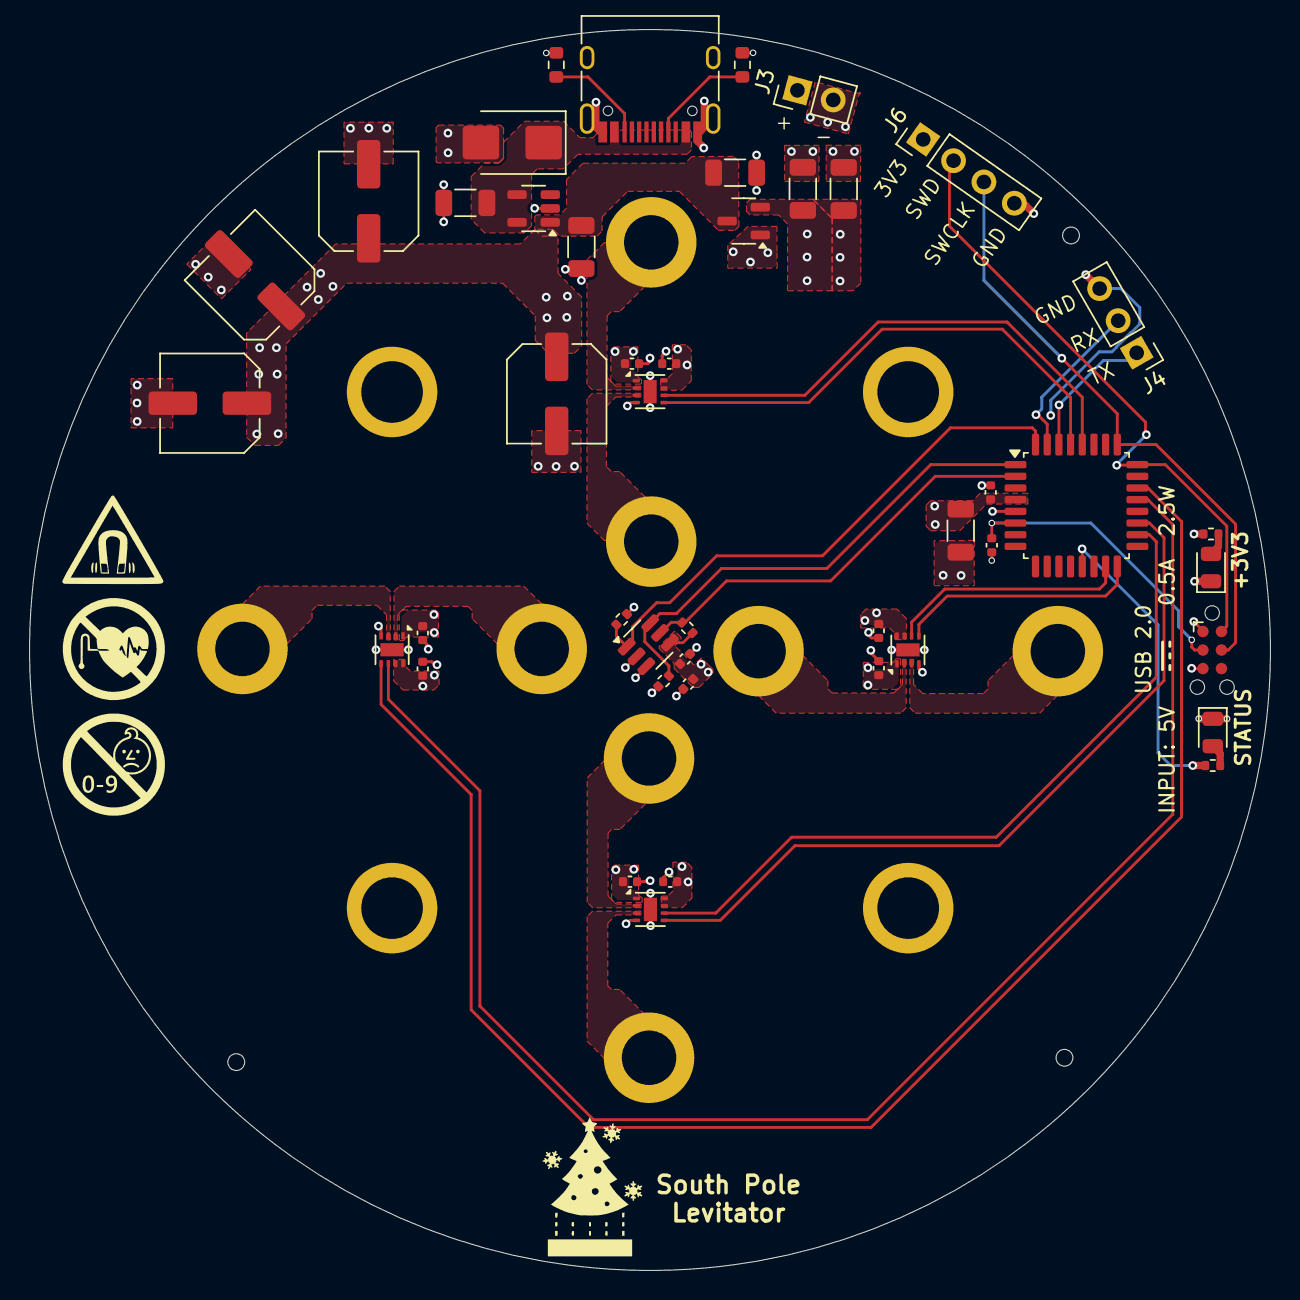
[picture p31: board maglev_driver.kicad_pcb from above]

Board: 4 copper layers, 85.0 x 85.0 mm, 65 parts (1 on the bottom side), 33 nets.

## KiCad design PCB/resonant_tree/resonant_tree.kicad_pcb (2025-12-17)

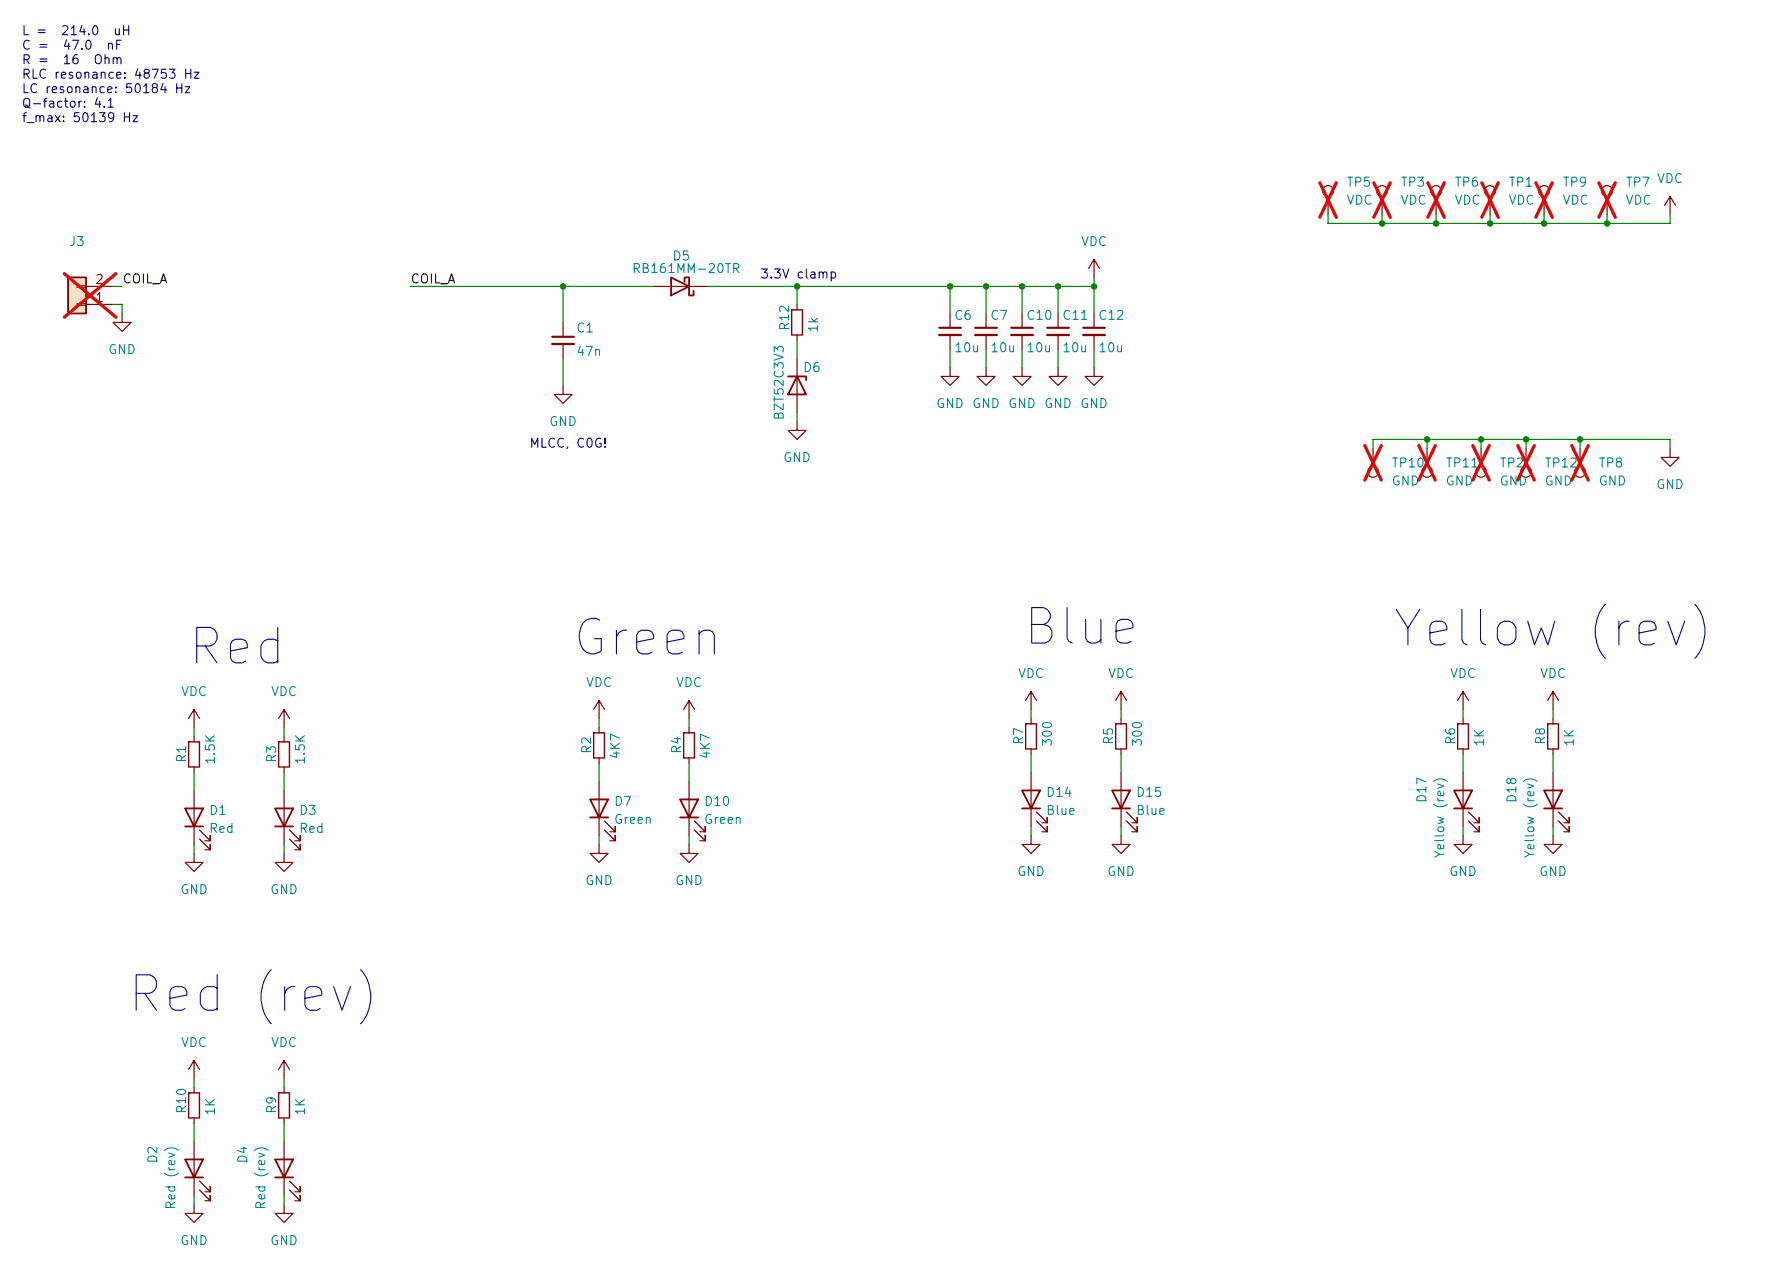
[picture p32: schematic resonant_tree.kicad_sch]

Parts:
C1: 47n; C_1206_3216Metric; MPN C21812
C6, C7, C10, C11, C12: 10u; C_1206_3216Metric; MPN C13585
D1, D3: Red; LED_0603_1608Metric; MPN C2286
D2, D4: Red (rev); LED_1206_3216Metric_ReverseMount_Hole1.8x2.4mm; MPN C125107
D5: RB161MM-20TR; D_SOD-123F; MPN C123070
D6: BZT52C3V3; D_SOD-123; MPN C19077396
D7, D10: Green; LED_0805_2012Metric; MPN C2297
D14, D15: Blue; LED_0603_1608Metric; MPN C2288
D17, D18: Yellow (rev); LED_1206_3216Metric_ReverseMount_Hole1.8x2.4mm; MPN C125108
J3: tree_link; not fitted
R1, R3: 1.5K; R_0603_1608Metric; MPN C22843
R2, R4: 4K7; R_0603_1608Metric; MPN C23162
R5, R7: 300; R_0603_1608Metric; MPN C23025
R6, R8, R9, R10: 1K; R_0603_1608Metric; MPN C21190
R12: 1k; R_0603_1608Metric; MPN C21190
TP1, TP3, TP5, TP6, TP7, TP9: VDC; TestPoint_Pad_D2.0mm; not fitted
TP2, TP8, TP10, TP11, TP12: GND; TestPoint_Pad_D2.0mm; not fitted

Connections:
/COIL_A: C1.1, D5.2 (A), J3.2
GND: C1.2, C6.2, C7.2, C10.2, C11.2, C12.2, D1.1 (K), D2.1 (K), D3.1 (K), D4.1 (K), D6.2 (A), D7.1 (K), D10.1 (K), D14.1 (K), D15.1 (K), D17.1 (K), D18.1 (K), J3.1, TP2.1, TP8.1, TP10.1, TP11.1, TP12.1
unnamed: D1.2 (A), R1.2
unnamed: D2.2 (A), R10.2
unnamed: D3.2 (A), R3.2
unnamed: D4.2 (A), R9.2
unnamed: D6.1 (K), R12.2
unnamed: D7.2 (A), R2.2
unnamed: D10.2 (A), R4.2
unnamed: D14.2 (A), R7.2
unnamed: D15.2 (A), R5.2
unnamed: D17.2 (A), R6.2
unnamed: D18.2 (A), R8.2
VDC: C6.1, C7.1, C10.1, C11.1, C12.1, D5.1 (K), R1.1, R2.1, R3.1, R4.1, R5.1, R6.1, R7.1, R8.1, R9.1, R10.1, R12.1, TP1.1, TP3.1, TP5.1, TP6.1, TP7.1, TP9.1

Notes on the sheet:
Red
MLCC, C0G!
Blue
3.3V clamp
Yellow (rev)
Green
Red (rev)
L = 214.0 uH C = 47.0 nF R = 16 Ohm RLC resonance: 48753 Hz LC resonance: 50184 Hz Q-factor: 4.1 f_max: 50139 Hz

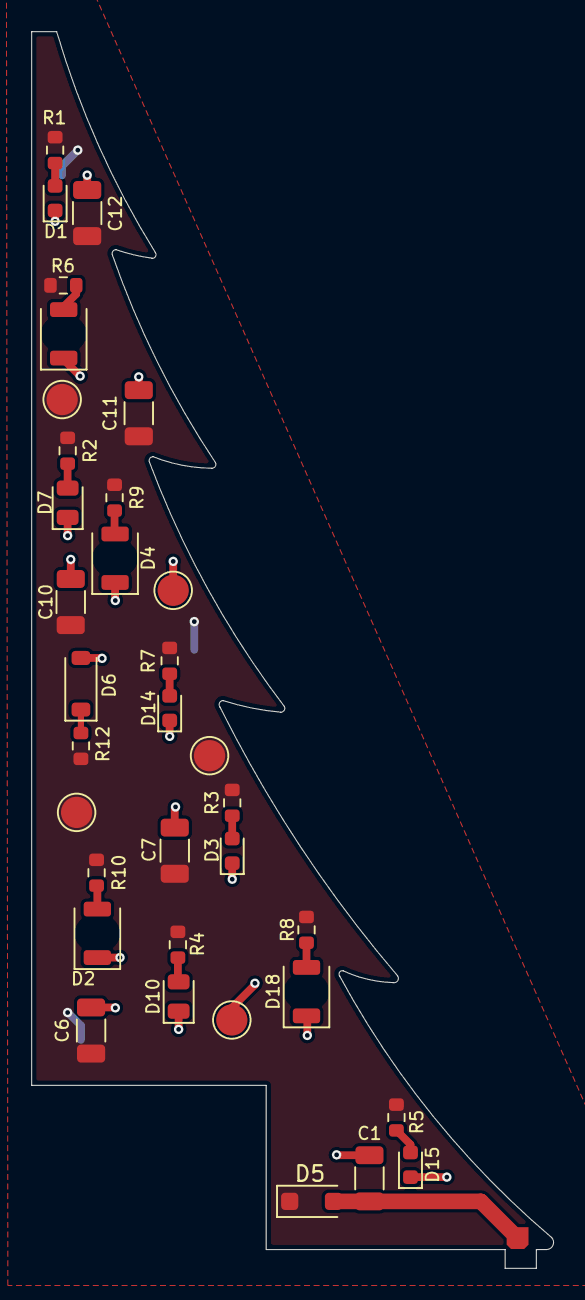
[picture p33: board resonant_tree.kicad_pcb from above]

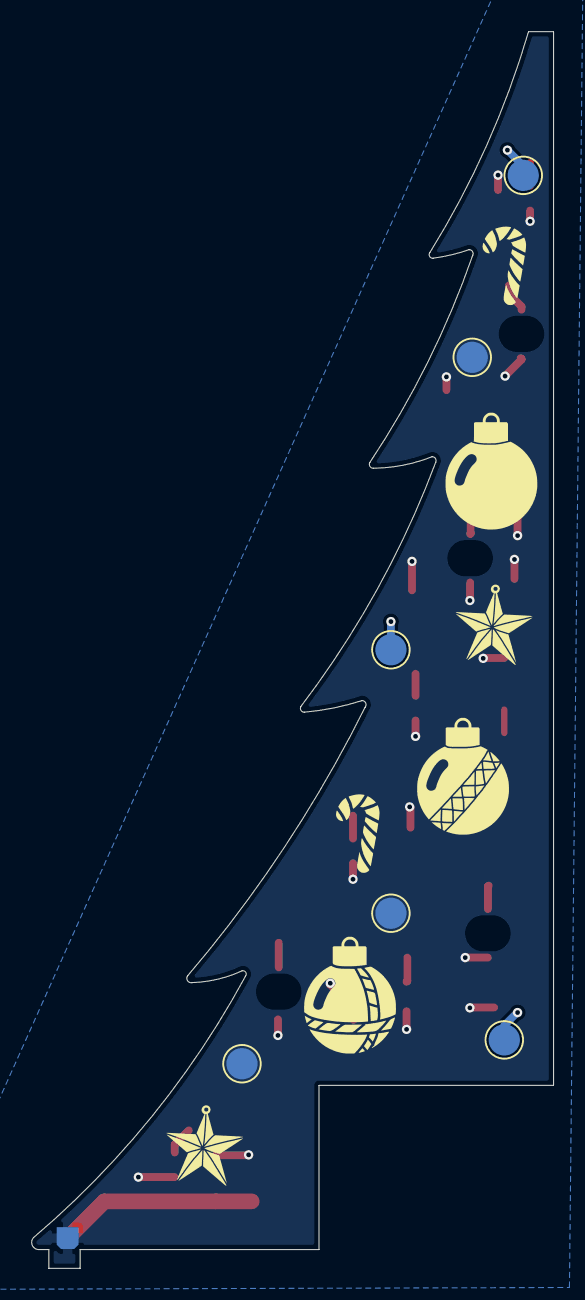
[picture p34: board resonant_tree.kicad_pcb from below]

Board: 2 copper layers, 33.4 x 79.1 mm, 41 parts (6 on the bottom side), 14 nets.

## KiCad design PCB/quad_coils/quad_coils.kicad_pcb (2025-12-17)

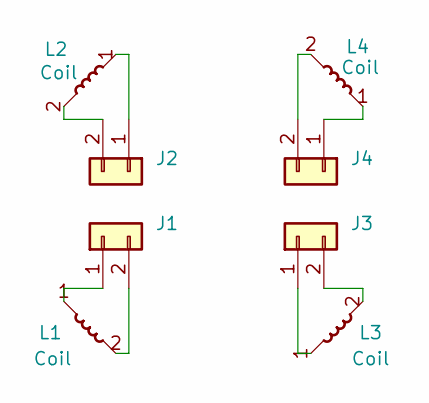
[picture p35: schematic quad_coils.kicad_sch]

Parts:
J1, J2, J3, J4: tree_mounting_point
L1, L2, L3, L4: Coil; 4L_100turns_33dia_0.3w

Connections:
unnamed: J1.1, L1.1
unnamed: J1.2, L1.2
unnamed: J2.1, L2.1
unnamed: J2.2, L2.2
unnamed: J3.1, L3.1
unnamed: J3.2, L3.2
unnamed: J4.1, L4.1
unnamed: J4.2, L4.2

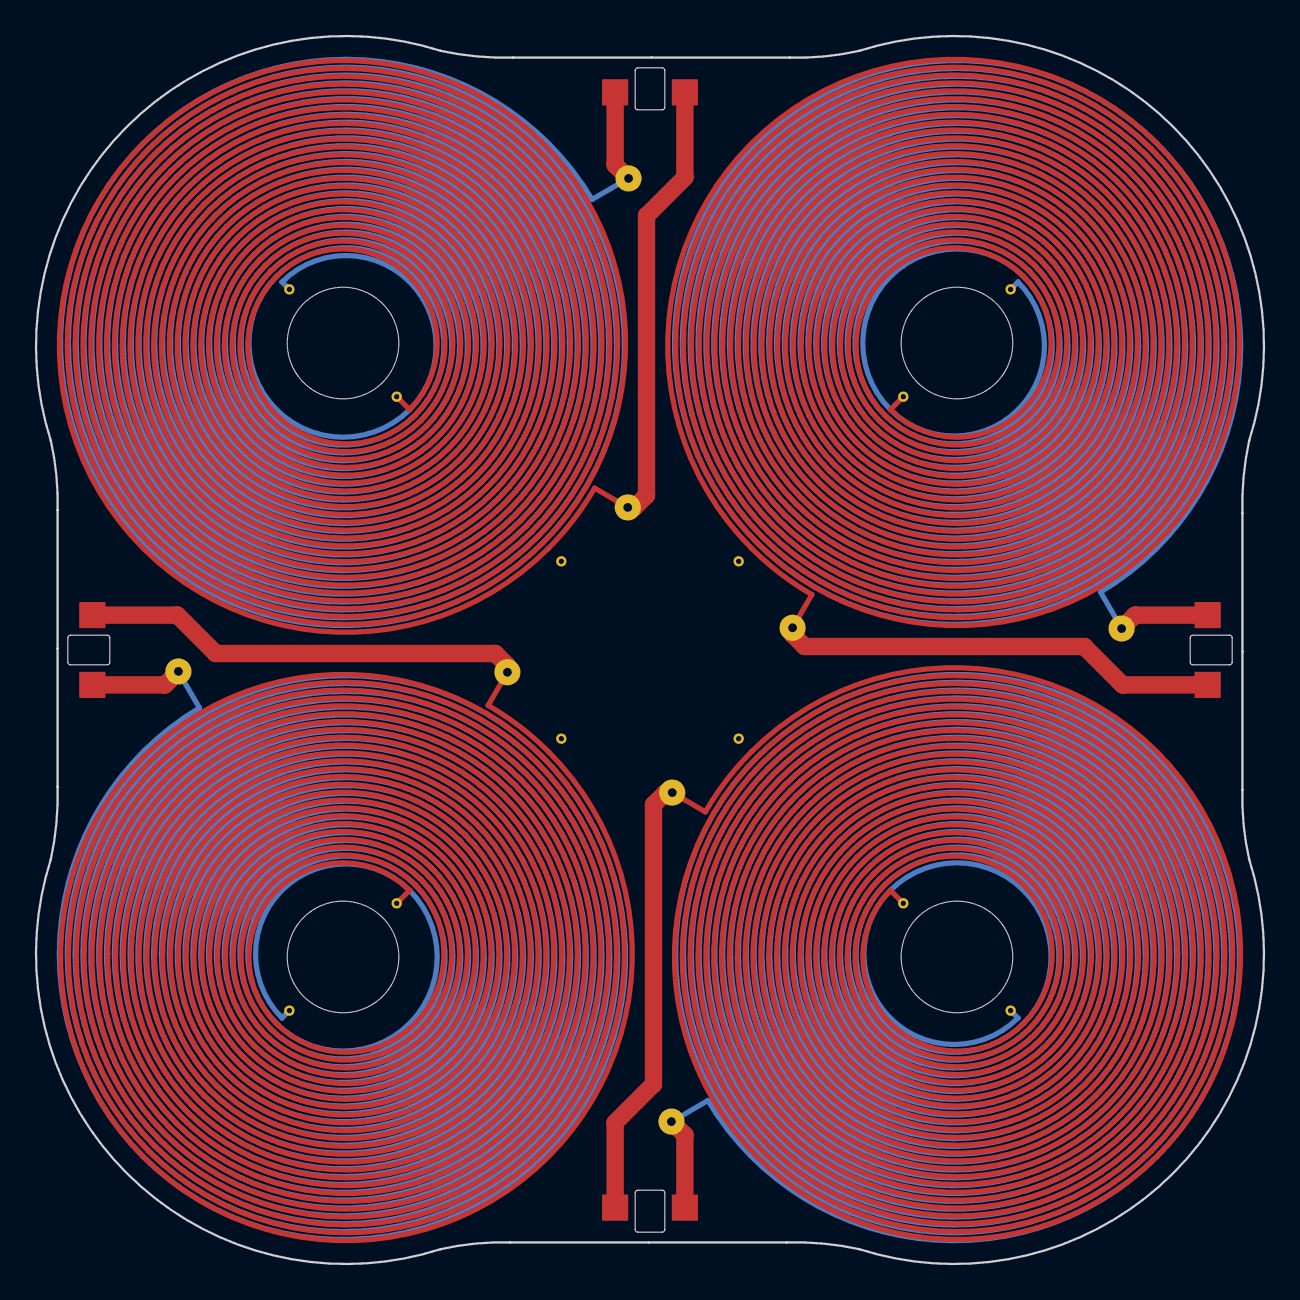
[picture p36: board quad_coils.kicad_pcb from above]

Board: 4 copper layers, 70.4 x 70.4 mm, 8 parts (0 on the bottom side), 8 nets.

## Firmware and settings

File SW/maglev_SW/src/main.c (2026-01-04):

#include "stm32g030xx.h"
#include "SEGGER_RTT.h"
#include "stdbool.h"
#include "stdlib.h"
#include "setup.h"
#include "TMAG5273.h"
#include "coils.h"
#include "filter.h"
#include "control.h"
#include "coil_cal.h"
#include "led.h"
#include "drive_linearization.h"

// Clamping
#define MIN(a,b) (((a)<(b))?(a):(b))
#define MAX(a,b) (((a)>(b))?(a):(b))
#define CLAMP(x, lower, upper) (MIN((upper), MAX((x), (lower))))

// Starting setpoint
#define START_SETPOINT_X 0
#define START_SETPOINT_Y 0

// Delay in ms before starting setpoint controller
#define SETPOINT_DELAY 2000

#define MAG_IDLE_XY_LIM 5000
#define MAG_IDLE_Z_LIM -3000

#define MAG_OP_XY_LIM 4000
#define MAG_OP_Z_LIM -1000

#define MAG_JINGLE_Z_LIM 30000



void _init(void) {}

typedef enum {
    INIT,
    CALIBRATION,
    IDLE,
    OPERATIONAL,
    TOO_HIGH_MAG_ERROR,
    JINGLE,
    ERROR,
} levitator_states_t;

levitator_states_t current_state = INIT;

biquad_t bqx;
biquad_t bqy;

PID_t pidx;
PID_t pidy;

setpoint_controller_t spc;

led_t status_led;

// IRQ variables
volatile uint32_t ms_tick = 0;  // global millisecond counter
volatile uint32_t us20_tick = 0;
volatile uint32_t run_filter = false;
volatile uint32_t run_ctrl = false;

// Sensor & Control variables
int16_t x, y, z;
int16_t offsets[2] = {0};
int32_t mag_from_coils_x;
int32_t mag_from_coils_y;

int16_t last_pwmx = 0;
int16_t last_pwmy = 0;
int32_t x_u_linearized = 0;
int32_t y_u_linearized = 0;
uint32_t setpoint_counter = 0;
uint32_t jingle_num;


// 5 kHz, Filter IRQ
void TIM14_IRQHandler(void)
{
    if (TIM14->SR & TIM_SR_UIF)
    {
        // Clear IRQ flag
        TIM14->SR &= ~TIM_SR_UIF;
        us20_tick++;
        run_filter = true;
    }
}

// 1 kHz, CTRL / LED IRQ
void TIM16_IRQHandler(void)
{
    if (TIM16->SR & TIM_SR_UIF)
    {
        // Clear IRQ flag
        TIM16->SR &= ~TIM_SR_UIF;
        led_Step(&status_led);
        ms_tick++;
        run_ctrl = true;
    }
}

// Systick
// void SysTick_Handler(void)
// {
    
// }

int main(void)
{
    setup_SystemClockInit();
    setup_I2CInit();
    // setup_SysTickEnable();

    // Filter init for X, Y fields
    filter_Biquad_Init(&bqx);
    filter_Biquad_Init(&bqy);

    // Control init
    control_PWM_Init(&pidx, 0);
    control_PWM_Init(&pidy, 0);
    control_Setpoint_Init(&spc, &pidx, &pidy, 0, 0);

    // Coil PWM init
    coils_TIM1_Init();
    coils_TIM3_Init();
    coils_ZeroDuty();

    // Segger RTT init
    SEGGER_RTT_Init();
    SEGGER_RTT_WriteString(0, "RTT ready\n");
    SEGGER_RTT_printf(0, "System Core Clock: %u \r\n", SystemCoreClock);

    // Sensor init
    TMAG5273_ISR_TIM14_Init();
    TMAG5273_Init();

    // Led init
    led_TIM16_Init();
    led_Setup(&status_led);
    led_ChangePattern(&status_led, OFF);
    led_IRQ_Init();

    // Coil calibration routine
    coil_cal_Init();

    #ifdef DEBUG_RTT
    SEGGER_RTT_WriteString(0, "Starting coil calibration...\n");
    bool header_printed = false;
    #endif

    while(1)
    {

        // 5 kHz filtering
        if (run_filter)
        {   
            TMAG5273_ReadXYZ(&x, &y, &z);
            coil_cal_CoilOffsets(fit_params, last_pwmx, -last_pwmx, last_pwmy, -last_pwmy, &mag_from_coils_x, &mag_from_coils_y);
            filter_Biquad_Step(&bqx, (int32_t) x - offsets[0] - mag_from_coils_x );
            filter_Biquad_Step(&bqy, (int32_t) y - offsets[1] - mag_from_coils_y );
            run_filter = false;
        }

        // 1 kHz control
        if (run_ctrl)
        {   

            switch (current_state)
            {
                //==================================================
                case INIT:
                    current_state = CALIBRATION;
                    led_ChangePattern(&status_led, RAMP);
                    break;
                
                //==================================================
                case CALIBRATION:
                    coil_cal_ZeroBias(offsets);
                    #ifdef DEBUG_RTT
                    SEGGER_RTT_printf(0, "Measured offsets: X: %d, Y: %d\r\n", offsets[0], offsets[1]);
                    #endif

                    if (abs(offsets[0]) > 1000 || abs(offsets[1]) > 1000)
                    {
                        current_state = TOO_HIGH_MAG_ERROR;
                        led_ChangePattern(&status_led, CONSTANT);
                        #ifdef DEBUG_RTT
                        SEGGER_RTT_WriteString(0, "Magnetic offsets too high, entering TOO_HIGH_MAG_ERROR state\r\n");
                        #endif
                        break;
                    }

                    int8_t result = coil_cal_MapPWM(fit_params, offsets);
                    if (result == -1)
                    {
                        current_state = TOO_HIGH_MAG_ERROR;
                        led_ChangePattern(&status_led, CONSTANT);
                        #ifdef DEBUG_RTT
                        SEGGER_RTT_WriteString(0, "Coil calibration failed, too high magnetic field detected, \
                                                    entering TOO_HIGH_MAG_ERROR state\r\n");
                        #endif
                        break;
                    }

                    current_state = IDLE;
                    led_ChangePattern(&status_led, BLINK);
                    // Play short jingle to indicate completion 
                    coils_Tone(0);
                    break;
                
                //==================================================    
                case TOO_HIGH_MAG_ERROR:
                    // Continue to check if magnetic field is still too high
                    coil_cal_ZeroBias(offsets);
                    if (abs(offsets[0]) <= 700 && abs(offsets[1]) <= 700)
                    {
                        current_state = CALIBRATION;
                        led_ChangePattern(&status_led, RAMP);
                        // Wait a bit before starting calibration
                        delay_ms(500);
                    }
                    break;

                //==================================================    
                case IDLE:
                    // Idle wait for magnet
                    // Reset regulators / integrators

                    #ifdef DEBUG_RTT
                    if (!header_printed) {
                        SEGGER_RTT_printf(0, "x_meas, y_meas, z_meas\r\n");
                        header_printed = true;
                    }
                    SEGGER_RTT_printf(0, "%6d, %6d, %6d\r", bqx.y[0], bqy.y[0], z);
                    #endif
                    // print debug info

                    // Enter operational if magnet is near center
                    if ((abs(bqx.y[0]) < MAG_OP_XY_LIM) && 
                        (abs(bqy.y[0]) < MAG_OP_XY_LIM) && 
                        (z < (MAG_OP_Z_LIM)) ) 
                    {
                        current_state = OPERATIONAL;
                        led_ChangePattern(&status_led, SINE);
                        control_Setpoint_Reset_Integral(&spc);
                        control_Setpoint_Init(&spc, &pidx, &pidy, START_SETPOINT_X, START_SETPOINT_Y);
                        setpoint_counter = 0;
                    }
                    // Play christmas jingle if upside down with tree on top.
                    else if (z > MAG_JINGLE_Z_LIM)
                    {   
                        current_state = JINGLE;
                        jingle_num = rand() % 4 + 1; // Random jingle (1-4)
                        led_ChangePattern(&status_led, CONSTANT);
                    }

                    break;

                //==================================================    
                case OPERATIONAL:
                    // Start setpoint controller after delay 
                    if (setpoint_counter >= SETPOINT_DELAY)
                    {
                        control_Setpoint_Step(&spc, bqx.y[0], bqy.y[0]);
                    }
                    else 
                    {
                        setpoint_counter++;
                    }

                    control_PWM_Step(&pidx, bqx.y[0]);
                    control_PWM_Step(&pidy, bqy.y[0]);

                    x_u_linearized = linearize_drive((int32_t)pidx.output);
                    y_u_linearized = linearize_drive((int32_t)pidy.output);

                    x_u_linearized  = CLAMP(x_u_linearized, -MAX_TIMER_VAL, MAX_TIMER_VAL);
                    y_u_linearized = CLAMP(y_u_linearized, -MAX_TIMER_VAL, MAX_TIMER_VAL);

                    coils_CalculateRMS(x_u_linearized, y_u_linearized); // Comment to disable dynamic PWM limiter
                    coils_LimitDuty(&x_u_linearized, &y_u_linearized);  // PWM limiter

                    coils_SetDuty(y_u_linearized, COIL_YP);
                    coils_SetDuty(-y_u_linearized, COIL_YN);

                    coils_SetDuty(x_u_linearized, COIL_XP);
                    coils_SetDuty(-x_u_linearized, COIL_XN);

                    last_pwmx = x_u_linearized;
                    last_pwmy = y_u_linearized;

                    // Exit to idle if magnet has been removed from center
                    if ((abs(bqx.y[0]) > MAG_IDLE_XY_LIM) || 
                        (abs(bqy.y[0]) > MAG_IDLE_XY_LIM) || 
                        (z > MAG_IDLE_Z_LIM) ) 
                    {
                        current_state = IDLE;
                        led_ChangePattern(&status_led, BLINK);
                        coils_ZeroDuty();
                        #ifdef DEBUG_RTT
                        header_printed = false;
                        #endif
                    }

                    #ifdef DEBUG_RTT
                    if (!header_printed) {
                        SEGGER_RTT_printf(0, "x_meas, y_meas, x_ref, y_ref, x_u, y_u, x_u_lin, y_u_lin\r\n");
                        header_printed = true;
                    }
                    SEGGER_RTT_printf(0, "%6d, %6d, %6d, %6d, %6d, %6d, %6d, %6d\r", 
                    bqx.y[0], bqy.y[0], pidx.ref, pidy.ref, pidx.output, pidy.output, x_u_linearized, y_u_linearized);
                    #endif
                    break;

                //==================================================
                case JINGLE:
                    // play christmas jingles
                    if (z < 10000)
                    {
                        current_state = IDLE;
                        led_ChangePattern(&status_led, BLINK);
                        break;
                    }
                    coils_Tone(jingle_num);
                    jingle_num = jingle_num % 4 + 1; // Increment 1 to 4
                    break;

                //==================================================
                case ERROR:
                    // indicate error with LED and stay here
                    break;
                    
                default:
                    break;
            }

            run_ctrl = false;
        }


    }

    __asm("NOP"); // how to inline assembly reminder
    return 0;
}

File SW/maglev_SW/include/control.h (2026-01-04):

#ifndef CONTROL_H
#define CONTROL_H

#include "stdint.h"
#include "filter.h"

#define Q_CTRL 13

#define Kp 5.5f
#define Kd 0.055f

#define CTRL_LOOP_FREQ 1000

// For now only uses P and D terms
typedef struct 
{
    int32_t output;
    int32_t error[2];
    int32_t derror;
    int32_t ref;
    int32_t KpQ;
    int32_t KdQ;
    int32_t fs;
} PID_t;

void control_PWM_Init(PID_t *pid, int32_t ref);
void control_PWM_Step(PID_t *pid, int32_t meas);

// Setpoint controller

#define SETPOINT_REF_Q 16
#define SETPOINT_REF_SHIFT  (1 << SETPOINT_REF_Q)

#define SETPOINT_INT_GAIN_DEFAULT  ((25 * SETPOINT_REF_SHIFT) / 10000)
#define SETPOINT_MAX_INT_STEP_ERROR_DEFAULT  ((5 * SETPOINT_REF_SHIFT) / 1000)
#define SETPOINT_ABS_INT_LIMIT_DEFAULT  (2500 * SETPOINT_REF_SHIFT)

typedef struct 
{
    int32_t int_x;
    int32_t int_y;
    int32_t int_gain;
    int32_t max_int_step_error;
    int32_t abs_int_limit;
    PID_t *pid_x;
    PID_t *pid_y;
    // Biquad filter
    biquad_t bq_sp_x;
    biquad_t bq_sp_y;
} setpoint_controller_t;

void control_Setpoint_Init(setpoint_controller_t *spc, PID_t *pid_x, PID_t *pid_y, int32_t sp_x, int32_t sp_y);
void control_Setpoint_Step(setpoint_controller_t *spc, int32_t error_x, int32_t error_y);
void control_Setpoint_Reset_Integral(setpoint_controller_t *spc);

#endif // CONTROL_H

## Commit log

2025-12-17 Add PCBs and CAD
    [bom.csv, coil_jig.stl, designators.csv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]
2026-01-03 Added driver board files
    [JS102011SAQN--3DModel-Eagle-1.STEP, SMTSO-M2-10ET-PennEngineering-3D-08-23-2025.stp, SMTSO-M2-3ET-PennEngineering-3D-05-11-2025.stp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]
2026-01-04 Add coil board
    [maglev_coils-B_Cu.gbr, maglev_coils-B_Mask.gbr, maglev_coils-B_Silkscreen.gbr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]

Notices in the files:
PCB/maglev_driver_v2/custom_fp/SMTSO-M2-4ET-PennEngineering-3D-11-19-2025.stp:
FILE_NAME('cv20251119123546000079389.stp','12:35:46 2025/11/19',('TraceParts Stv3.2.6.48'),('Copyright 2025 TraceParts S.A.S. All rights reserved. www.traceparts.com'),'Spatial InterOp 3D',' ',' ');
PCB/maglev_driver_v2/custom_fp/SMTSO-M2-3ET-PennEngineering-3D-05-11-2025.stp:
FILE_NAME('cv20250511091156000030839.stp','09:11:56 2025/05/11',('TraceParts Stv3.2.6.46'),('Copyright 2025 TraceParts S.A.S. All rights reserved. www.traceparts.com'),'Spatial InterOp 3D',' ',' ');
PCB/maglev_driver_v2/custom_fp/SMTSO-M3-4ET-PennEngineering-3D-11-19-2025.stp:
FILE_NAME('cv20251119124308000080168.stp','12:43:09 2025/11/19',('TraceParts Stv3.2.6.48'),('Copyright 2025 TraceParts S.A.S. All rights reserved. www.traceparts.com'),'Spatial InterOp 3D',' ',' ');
